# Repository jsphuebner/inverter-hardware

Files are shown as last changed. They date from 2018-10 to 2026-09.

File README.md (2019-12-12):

# inverter-hardware
Eagle schematics of inverter main board, sensor boards and gate drivers

# License
Attribution-ShareAlike 4.0 International
https://creativecommons.org/licenses/by-sa/4.0/legalcode

You musn't change the copyright info (J. Huebner and openinverter.org) on the silkscreen in size location or content.

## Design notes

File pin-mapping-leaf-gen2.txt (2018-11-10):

Connection diagram of CN001
Diagram found here: http://productions.8dromeda.net/c55-leaf-inverter-protocol.html
+-----------------------------------+  +------------+
| 47   46   21 20 19 18 17 16 15 14 |  |       x  x |
|           29 28 27 26 25  x 23 22 |  |  6 x  x  x |
| 49   48    x  x  x  x  x  x  x  x |  | 10 x  x  x |
|           45 44 43 42 41 40 39 38 |  |    x  x  x |
+-----------------------------------+  +------------+

- 6 = OUT_BRAKE
- 10 = IN_BMS
- 14 = CANH *
- 15 = CANL *
- 16 = IN_FORWARD
- 17 = RES_S2 *
- 18 = RES_S4 *
- 19 = RES_R1 *
- 20 = RES_S1 *
- 21 = RES_S3 *
- 22 = IN_START
- 23 = IN_BRAKE
- 25 = IN_REVERSE
- 26 = 5V
- 27 = RES_R2 (GND) *
- 28 = THROTTLE2
- 29 = THROTTLE1
- 38 = IN_CRUISE
- 39 = OUT_PWM
- 40 = OUT_ERR
- 41 = OUT_OVTG
- 42 = OUT_DCSW * (! 12V input on original harness, make sure not to connect to 12V but to DC switch!)
- 43 = OUT_PRE
- 44 = MTEMP1 *
- 45 = MTEMP2 *
- 46 = 12V *
- 47 = GND *
- 48 = 12V *
- 49 = GND *
Only pins with * are populated on the OEM wire harness

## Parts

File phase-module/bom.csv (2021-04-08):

Ref | Part | Value | Remarks
IC1,IC2 | 1ED3124MU12HXUMA1
C1, C2, C3, C5 | C0603 | 1uF
D1 | SMB | CMR1-10 TR13 PBFREE | Any high voltage diode 1A
R1,R2,R3,R4,R6,R7,R9,R10 | R0603 | 10Ω | Gate resistors, application dependent
IC3 | MLX91206LDC-CAH-004-TU
R5 | R0603 | 3k3
R8 | R0603 | 6k8 | Not needed on V3 mainboards

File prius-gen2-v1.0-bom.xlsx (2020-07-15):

Designator | Comment | Package | LCSC Part #
ALIVE, PWR | LED_0603_GN | CHIPLED-0805 | C84256
C7, C22, C27, C33, C43 | 10uF | C0805 | C15850
C1, C2, C3, C35, C36 | 1nF | C0603 | C46653
C13, C23 | 100uF | SMD-ECAP-6.3X7.7 | C176675 | e
C28, C30 | 22p | C0603 | C1804
C4, C5, C6, C8, C9, C10, C11, C12, C14, C15, C16, C17, C18, C20, C21, C24, C25, C37, C41, C42 | 1uF | C0603 | C28323
C19, C26, C29, C31, C32, C34 | 22n | C0603 | C21122
D1, D2 | CDBA540-HF | SMB | C22452
IC7 | MP2359DJ-LF-Z | TSOT-23-6 | C14259
IC3 | TDA2822D | SO08 | C73296 | e
IC5 | SN65HVD230 | SO08 | C12084
IC1 | STM32F103RBT6 | LQFP-64_10.0x10.0x0.5P | C8735
IC6 | ULN2003AD | SO16 | C7512
IC4 | MCP6002T-I/SN | SO08 | C7377
IC2 | AMS1117-3.3 | SOT-223 | C6186
L2, L3 | 10uH | L0805 | C1046
L1 | 6.8uH | L1210 | C87559 | e
Q3 | 8MHz | SMD-5032_2P | C115962
R19 | 220Ω | R0603 | C22962
R12, R14, R15, R20, R25 | 1.2KΩ | R0603 | C22765
R1, R2, R13, R16, R21, R32, R33 | 510Ω | R0603 | C23193
R8, R9, R10, R17, R18, R22, R23, R24, R27, R30, R35, R40, R50, R51, R52, R53, R54, R55, R56 | 10KΩ | R0603 | C17414
R3, R4, R6, R7, R29, R31, R34 | 3.3KΩ | R0603 | C26010
R5, R11 | 4.7KΩ | R0603 | C17673
R42, R49 | 4.7Ω | R0603 | C23164
R26, R36, R37, R38, R39, R47, R48 | 100kΩ | R0603 | C25803
R28 | 56kΩ | R0603 | C23206
Q1, Q2 | AP9T18GH-HF | TO-252-2 | C124546 | e
C38, C39 | 100nF | C0603 | C14663
R44, R46 | 15kΩ | R0603 | C22809
R43, R45 | 33kΩ | R0603 | C4216
R41 | 120Ω | R0603 | C22787

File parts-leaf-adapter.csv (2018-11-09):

Name | Value | Part #
C1 | 1µ
C2 | 1µ
CN001 |  | 1939561-3 (unobtanium - salavage needed)
CN101 |  | GT8E-5P-DS
CN151 |  | GT8E-12DP-DS
CN501 |  | GT8E-16DP-DS
CN601 |  | GT8E-8P-DS
IC1 | 74*00
R1 | 120
R2 | 10k
R3 | 10k
R4 | 10k
R5 | 10k
R7 | 47k
R8 | 47k
R9 | 1k
R10 | 1k

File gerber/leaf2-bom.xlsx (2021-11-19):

Designator | Comment | Package | LCSC Part #
C1, C2 | 1uF | C0805 | C28323
IC1 | MC74HC1G08 | SOT-23-5 | C108694
R2, R3, R4, R5 | 10KΩ | R0603 | C17414
R7, R8 | 47KΩ | R0603 | C25819
R9, R10 | 1.2KΩ | R0603 | C22765

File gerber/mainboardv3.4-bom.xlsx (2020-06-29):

Designator | Comment | Package | LCSC Part #
ALIVE, PWR | LED_0603_GN | CHIPLED-0805 | C84256
C1, C2, C22, C46 | 10uF | C0805 | C15850
C11, C12, C12, C38, C41, C42 | 1nF | C0603 | C46653
C8 | 470uF | SMD-ECAP-10x10 | C176672 | e
C20 | 470uF | SMD-ECAP-6.3X7.7 | C134738 | e
C45 | 330uF | SMD-ECAP-6.3X7.7 | C134823 | e
C26, C27 | 22p | C0603 | C1804
C3, C4, C5, C6, C7, C9, C10, C13, C14, C15, C16, C17, C19, C21, C23, C24, C25, C28, C29, C30, C31, C32, C33, C39, C40, C43, C48 | 1uF | C0603 | C28323
C34, C35, C36, C37, C44, C47 | 22n | C0603 | C21122
D1, D2 | CDBA540-HF | SMB | C22452
D3 | SBR1A40S3-7 | SOD-323F | C2128
IC1 | LM2596S | TO263-5 | C10002
IC2 | TDA2822D | SO08 | C73296 | e
IC3 | SN65HVD230 | SO08 | C12084
IC4 | STM32F103RBT6 | LQFP-64_10.0x10.0x0.5P | C8735
IC5 | MIC2288YD5 | SOT23-5L | C7722
IC6 | ULN2003AD | SO16 | C7512
IC7 | LM2901 | SO14 | C142961 | e
IC8 | AMS1117-3.3 | SOT-223 | C6186
IC9 | SN74LVC1G10 | SOT-23-6 | C258149 | e
L1, L3 | 10uH | L0805 | C1046
L4 | 10uH | L1210 | C86069 | e
L2 | 47uH | SMD-PIND-12.5x12.5x8_2.9x5.4 | C169389 | e
Q1 | 8MHz | SMD-5032_2P | C115962
R1 | 220Ω | R0603 | C22962
R10, R12, R13, R19, R23, R26, R27, R29 | 1.2KΩ | R0603 | C22765
R11, R15, R16, R17, R18, R32, R33, R36, R40 | 510Ω | R0603 | C23193
R14,R20, R21, R22, R24, R25, R31, R37, R38, R39, R41, R43, R45, R46, R47 | 10KΩ | R0603 | C17414
R2, R3, R3, R4, R6, R7, R8, R9, R35, R42, R44, R48, R49 | 3.3KΩ | R0603 | C26010
R5, R50, R51 | 4.7KΩ | R0603 | C17673
R52 | 10Ω | R0603 | C22859
T1 | AP9T18GH-HF | TO-252-2 | C124546 | e

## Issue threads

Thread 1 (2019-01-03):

Gate driver missing

alberto-cesare, 2019-01-03:
Hi Johannes,

thanks for sharing this amazing work.
I noticed that gate driver board, schematic and bom is missing from the repo.
I found the schematic on your site, but there is no name for the DC/DC converter and the pcb.
Can you please upload this design?

Many many thanks!
Alberto

jsphuebner, 2019-01-03:
Hi Alberto,

thanks for pointing it out. I added the part numbers and uploaded the files to the repo.

Johannes

Closed 2019-01-03.

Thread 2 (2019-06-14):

Revision 3

gimbas, 2019-06-14:
Greetings, i was under the impression you made your Revision 3 leaf adapter boards open source also, will the design files be available?
I was looking for the pinout of the leaf inverter connectors.

jsphuebner, 2019-07-25:
The design files vor Rev3 main board will be released as soon as I have sold off my stock.
The adapter board is leaf_adapter.fpc and opens with https://www.freepcb.com/

Closed 2019-12-29.

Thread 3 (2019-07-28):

Add License file

DOSputin, 2019-07-28:
A `LICENSE` including the full language of the chosen licensing scheme should be included as a separate file in the code repository.

DOSputin, 2019-07-28:
Reading the CC license, it says

> indicate the Licensed Material is licensed under this Public License, and include the text of, or the URI or hyperlink to, this Public License.

So it seems that putting the link the readme satisfies this particular license terms.

will close issue now.

jsphuebner, 2019-07-28:
Very good, less to do :) Thanks.

Closed 2019-07-28.

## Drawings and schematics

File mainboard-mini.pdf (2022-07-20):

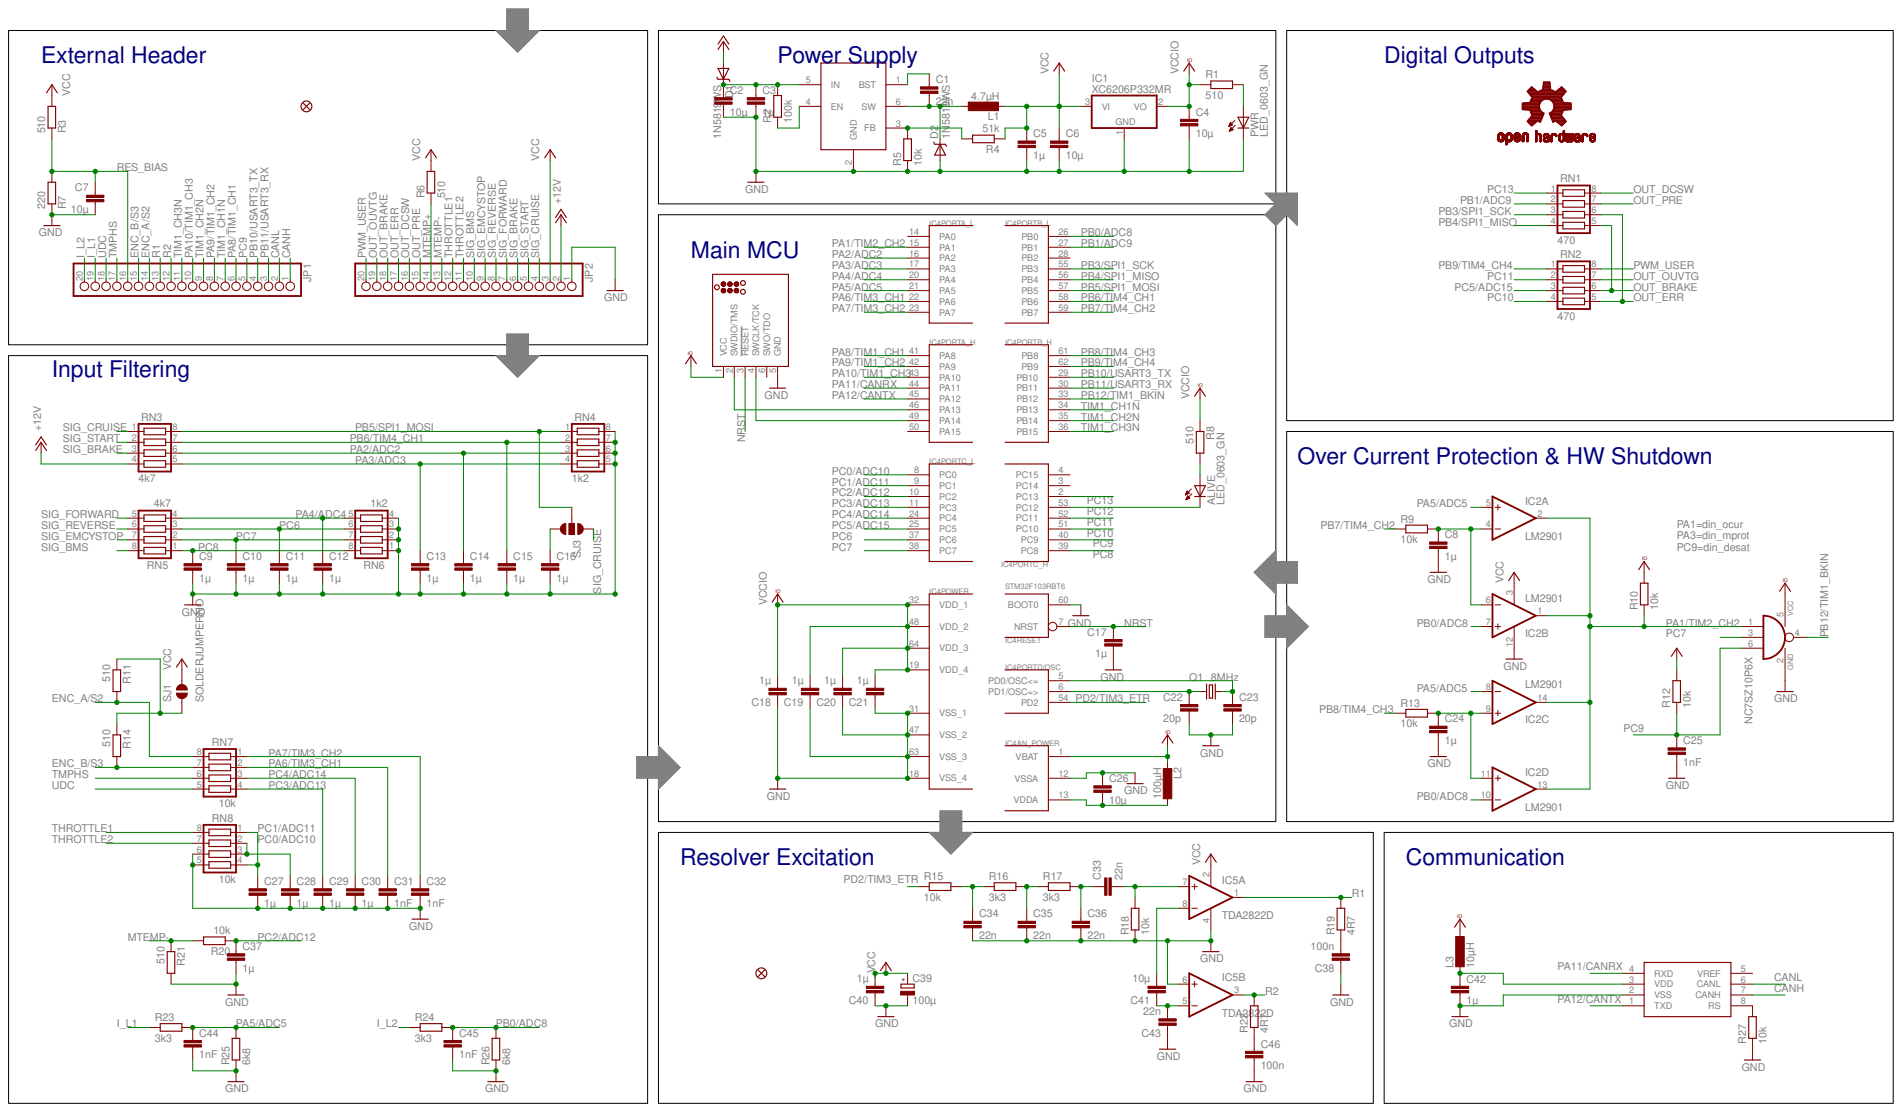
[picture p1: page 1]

IO Over Current Protection & HW Shutdown

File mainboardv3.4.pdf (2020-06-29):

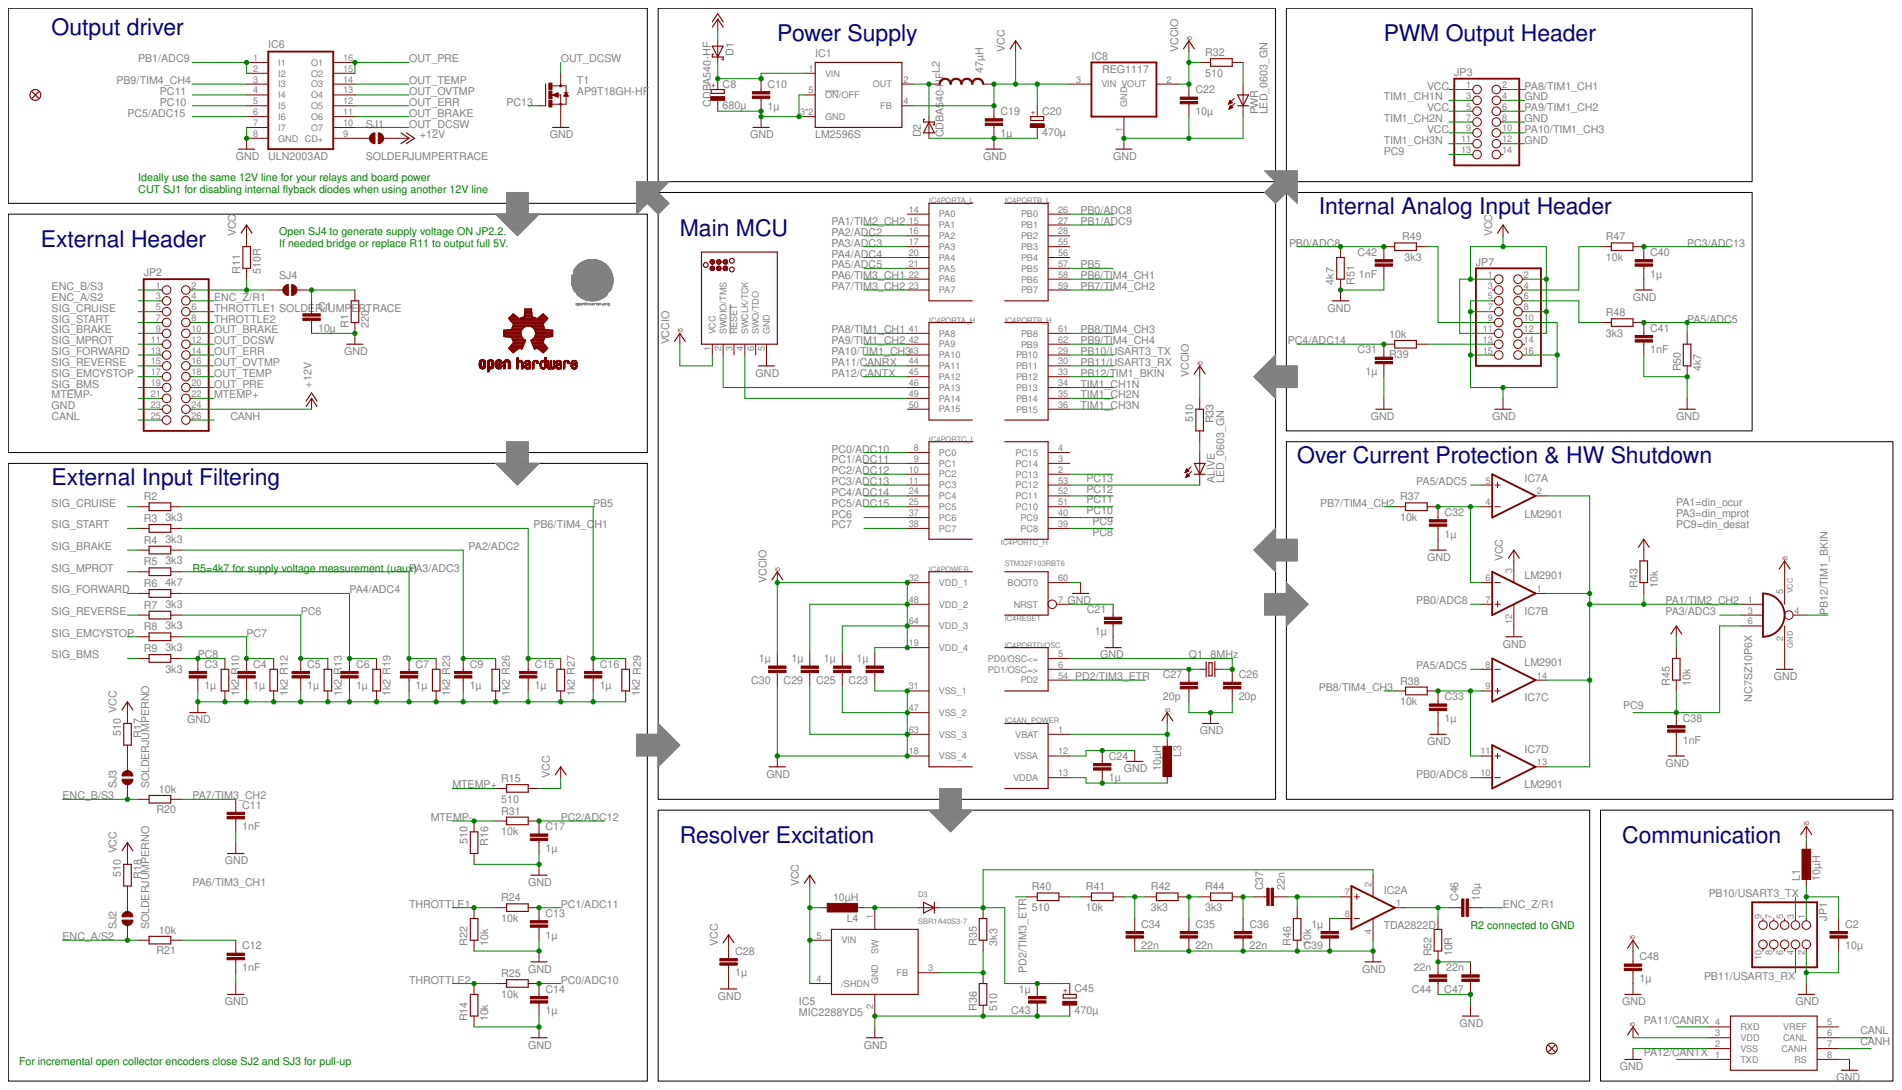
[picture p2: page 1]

Ideally use the same 12V line for your relays and board power CUT SJ1 for disabling internal flyback diodes when using another 12V line

Internal Analog Input Header

Open SJ4 to generate supply voltage ON JP2.2.
If needed bridge or replace R11 to output full 5V.

Over Current Protection & HW Shutdown

For incremental open collector encoders close SJ2 and SJ3 for pull-up

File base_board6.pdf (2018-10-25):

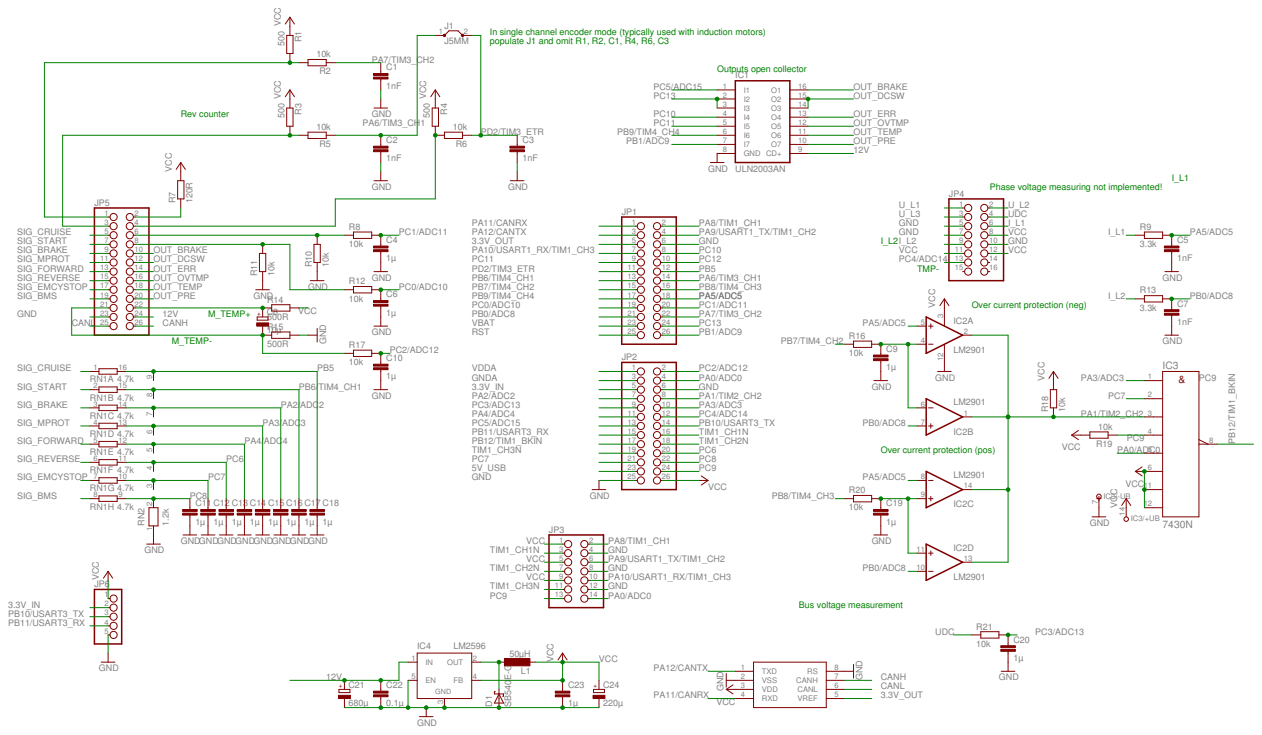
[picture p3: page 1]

In single channel encoder mode (typically used with induction motors) populate J1 and omit R1, R2, C1, R4, R6, C3

Phase voltage measuring not implemented!

Over current protection (pos)

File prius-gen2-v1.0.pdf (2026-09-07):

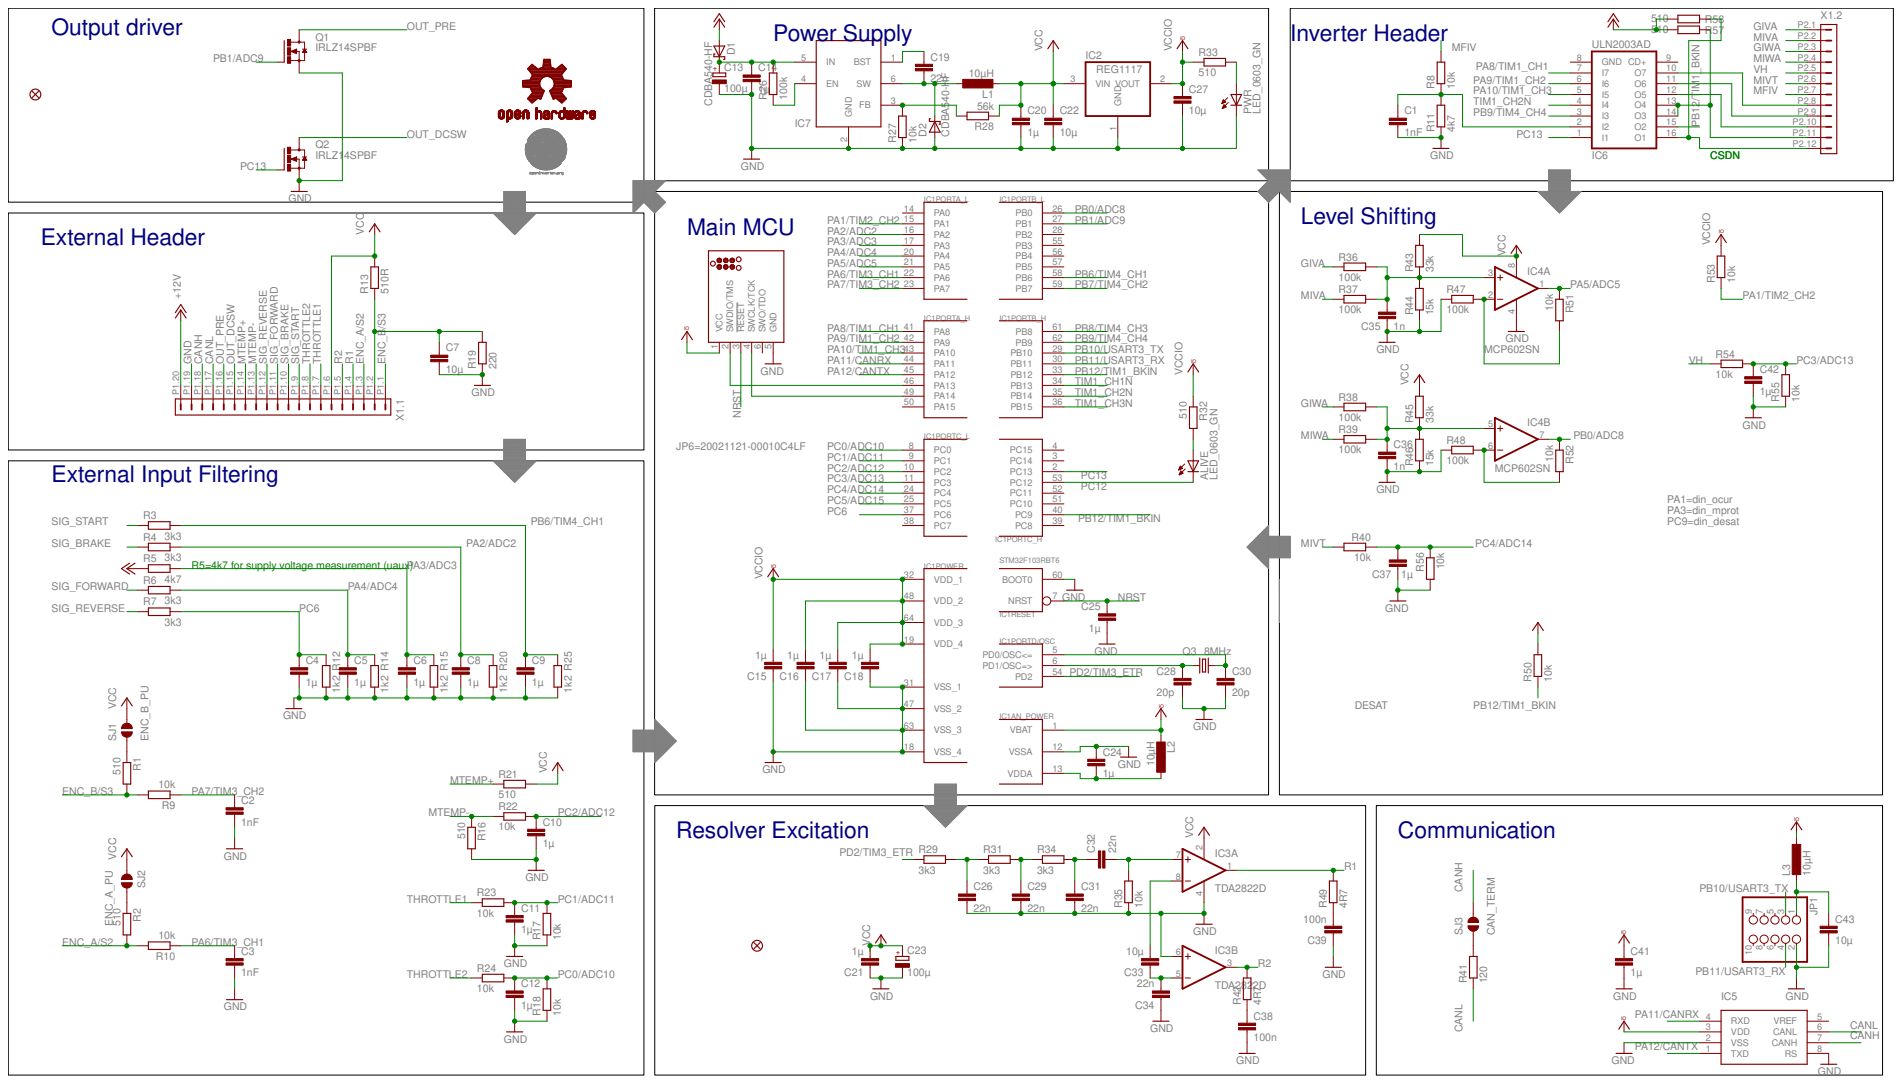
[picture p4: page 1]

Level Shifting Main MCU

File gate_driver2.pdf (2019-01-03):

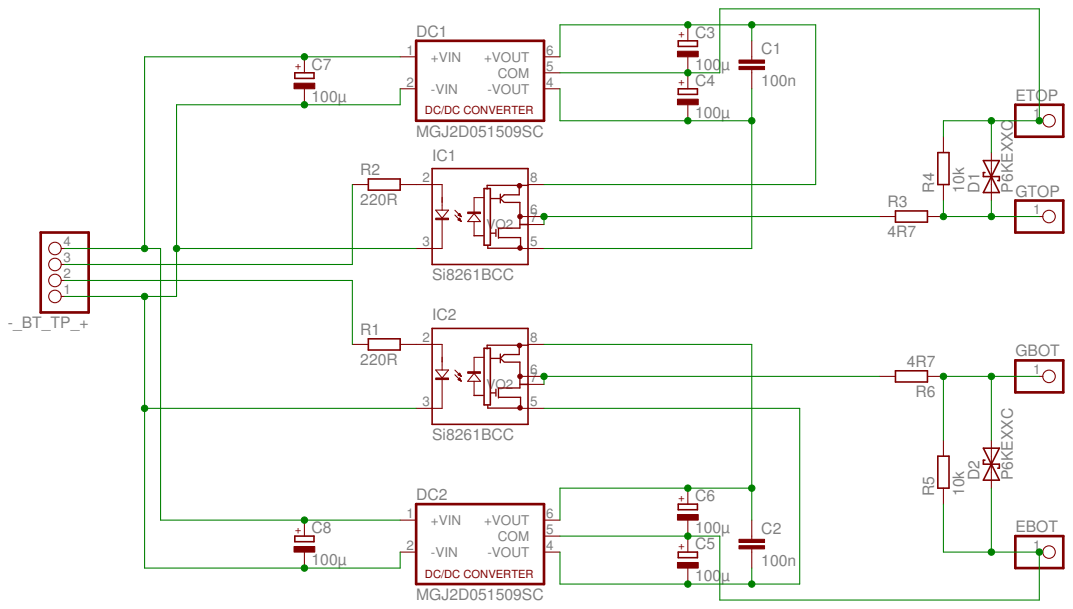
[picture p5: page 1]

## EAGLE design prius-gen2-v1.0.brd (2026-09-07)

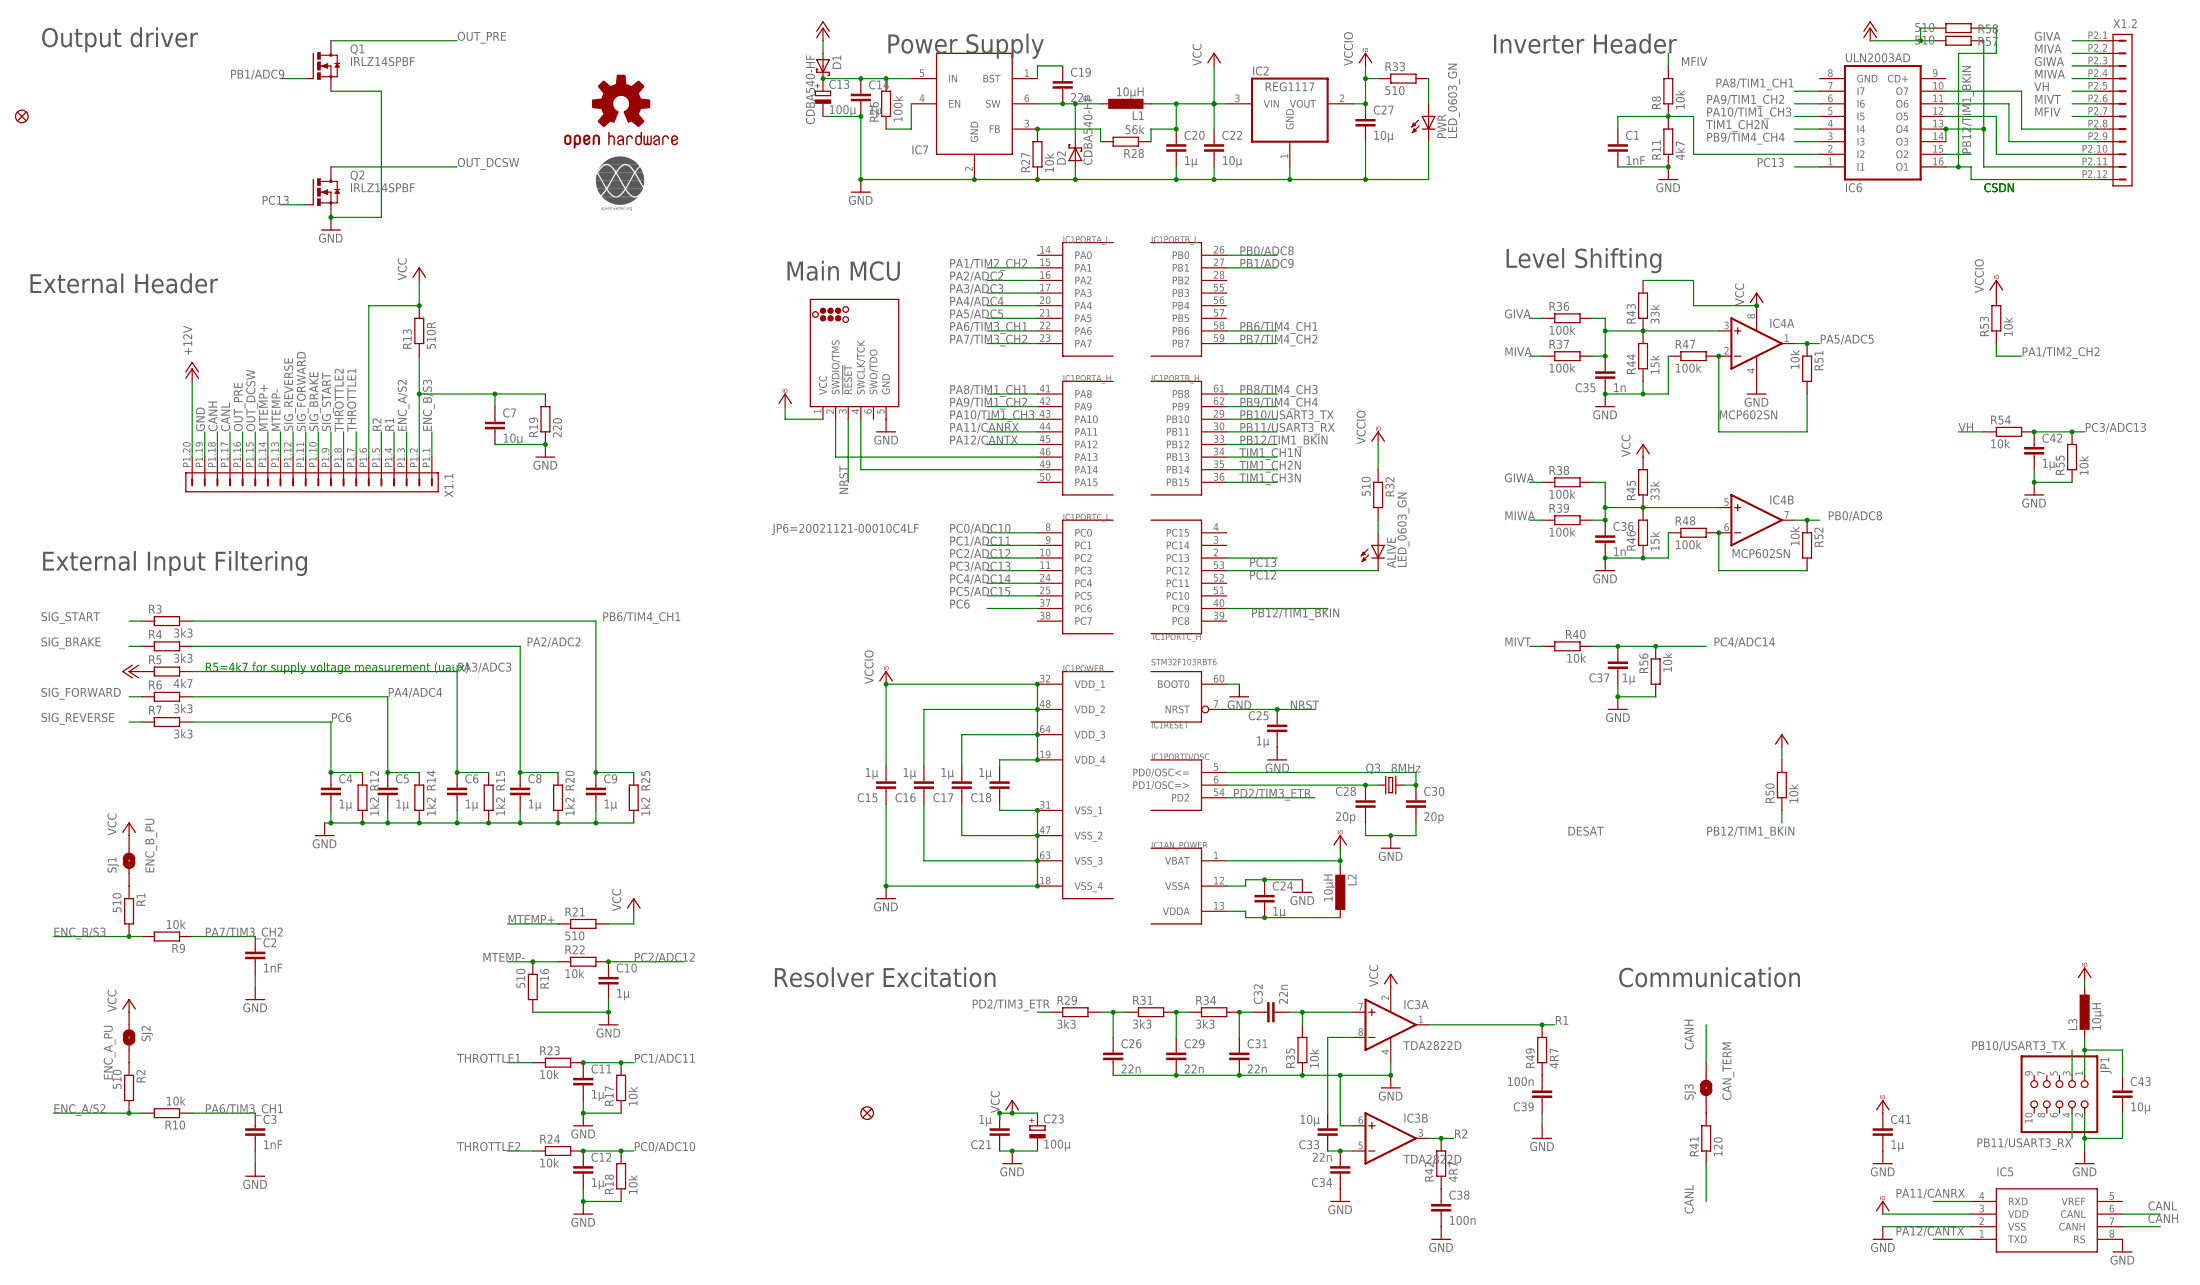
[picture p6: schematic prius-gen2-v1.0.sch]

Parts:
ALIVE: LED_0603_GN; SML0805
C1, C2, C3: 1nF; C0603
C4, C5, C6, C8, C9, C10, C11, C12, C14, C15, C16, C17, C18, C20, C21, C24, C25, C37, C41, C42: 1µ; C0603
C7, C22, C27, C33, C43: 10µ; C0805
C13, C23: 100µ; UD-6,3X7,7_NICHICON
C19, C26, C29, C31, C32, C34: 22n; C0603
C28, C30: 20p; C0603
C35, C36: 1n; C0603
C38, C39: 100n; C0603
D1, D2: CDBA540-HF; SMB
FID1, FID2: FIDUCIAL1X2.5; FIDUCIAL-1X2.5
IC1: STM32F103RBT6; TQFP64
IC2: REG1117; SOT223
IC3: TDA2822D; SO08
IC4: MCP602SN; SO08
IC5: SN65HVD230; SO08
IC6: ULN2003AD; SO16
IC7: MB2359DJ; SOT23-6
J1: TC2030_SWD-MCP; TC2030-MCP
JP1: PINHD-2X5/90; 2X05/90
L1: 10µH; L2825P
L2, L3: 10µH; L2012C
LOGO1: OSHW-LOGOM; OSHW-LOGO-M
PWR: LED_0603_GN; SML0805
Q1, Q2: IRLZ14SPBF; D-PAK_TO252AA
Q3: 8MHz; CRYSTAL-TXC-7A
R1, R2, R16, R21, R32, R33, R57, R58: 510; R0603
R3, R4, R6, R7, R29, R31, R34: 3k3; R0603
R5, R11: 4k7; R0603
R8, R9, R10, R17, R18, R22, R23, R24, R27, R35, R40, R50, R51, R52, R53, R54, R55, R56: 10k; R0603
R12, R14, R15, R20, R25: 1k2; R0603
R13: 510R; R0603
R19: 220; R0603
R26, R36, R37, R38, R39, R47, R48: 100k; R0603
R28: 56k; R0603
R41: 120; R0603
R42, R49: 4R7; R0603
R43, R45: 33k; R0603
R44, R46: 15k; R0603
SJ1: ENC_B_PU; SJ_2S-NO
SJ2: ENC_A_PU; SJ_2S-NO
SJ3: CAN_TERM; SJ_2S-NO
U$1: OI-LOGO; OI_LOGO
X1: 5810132011

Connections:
+12V: D1.A, R5.1, R57.1, R58.1, X1.P1.20 (20)
CANH: IC5.7 (CANH), SJ3.2, X1.P1.18 (18)
CANL: IC5.6 (CANL), R41.1, X1.P1.17 (17)
ENC_A/S2: R2.2, R10.2, X1.P1.3 (3)
ENC_B/S3: R1.2, R9.2, X1.P1.1 (1)
GIVA: R36.1, X1.P2.1 (1)
GIWA: R38.1, X1.P2.3 (3)
GND: C1.2, C2.2, C3.2, C4.2, C5.2, C6.2, C7.2, C8.2, C9.2, C10.2, C11.2, C12.2, C13.-, C14.2, C15.1, C16.1, C17.1, C18.1, C20.2, C21.1, C22.2, C23.-, C24.1, C25.2, C26.2, C27.2, C28.2, C29.2, C30.2, C31.2, C34.1, C35.2, C36.2, C37.2, C38.2, C39.1, C41.2, C42.2, C43.2, D2.A, IC1.12 (VSSA), IC1.18 (VSS_4), IC1.31 (VSS_1), IC1.47 (VSS_2), IC1.60 (BOOT0), IC1.63 (VSS_3), IC2.1 (GND), IC3.4 (V-), IC3.6 (+IN), IC4.4 (V-), IC5.2 (VSS), IC5.8 (RS), IC6.8 (GND), IC7.2 (GND), J1.5 (GND), JP1.2, PWR.C, Q1.3 (S), Q2.3 (S), R11.1, R12.1, R14.1, R15.1, R16.2, R17.1, R18.1, R19.1, R20.1, R25.1, R27.1, R35.1, R44.1, R46.1, R47.1, R48.1, R55.1, R56.2, X1.P1.19 (19)
MFIV: R8.2, X1.P2.7 (7)
MIVA: R37.1, X1.P2.2 (2)
MIVT: R40.2, X1.P2.6 (6)
MIWA: R39.1, X1.P2.4 (4)
MTEMP+: R21.1, X1.P1.14 (14)
MTEMP-: R16.1, R22.1, X1.P1.13 (13)
unnamed: IC6.12 (O5), X1.P2.10 (10)
unnamed: C28.1, IC1.6 (PD1/OSC=>), Q3.P$1 (1)
unnamed: C13.+, C14.1, D1.C, IC7.5 (IN), R26.2
unnamed: C30.1, IC1.5 (PD0/OSC<=), Q3.P$2 (2)
unnamed: C19.1, IC7.1 (BST)
unnamed: IC1.46 (PA13), J1.2 (SWDIO/TMS)
unnamed: C24.2, IC1.13 (VDDA), L2.1
unnamed: IC7.4 (EN), R26.1
unnamed: IC1.49 (PA14), J1.4 (SWCLK/TCK)
unnamed: C33.1, C34.2, IC3.5 (-IN)
unnamed: C39.2, R49.1
unnamed: C33.2, IC3.8 (-IN)
unnamed: IC7.3 (FB), R27.2, R28.2
unnamed: C19.2, D2.C, IC7.6 (SW), L1.1
unnamed: IC6.11 (O6), X1.P2.9 (9)
unnamed: IC6.10 (O7), X1.P2.8 (8)
unnamed: C29.1, R31.2, R34.1
unnamed: C31.1, C32.1, R34.2
unnamed: C32.2, IC3.7 (+IN), R35.2
unnamed: R2.1, SJ2.2
unnamed: R1.1, SJ1.1
unnamed: PWR.A, R33.2
unnamed: ALIVE.A, R32.2
unnamed: C1.1, IC6.2 (I2), R8.1, R11.2
unnamed: IC6.16 (O1), R58.2, X1.P2.12 (12)
unnamed: R41.2, SJ3.1
unnamed: C38.1, R42.1
unnamed: C43.1, JP1.1, L3.2
unnamed: IC6.13 (O4), IC6.14 (O3), R57.2, X1.P2.11 (11)
unnamed: C26.1, R29.2, R31.1
unnamed: C36.1, IC4.5 (+IN), R38.2, R39.2, R45.1, R46.2
unnamed: C35.1, IC4.3 (+IN), R36.2, R37.2, R43.1, R44.2
unnamed: IC4.2 (-IN), R47.2, R51.2
unnamed: IC4.6 (-IN), R48.2, R52.2
NRST: C25.1, IC1.7 (NRST), J1.3 (!RESET)
OUT_DCSW: Q2.4 (D), X1.P1.15 (15)
OUT_PRE: Q1.4 (D), X1.P1.16 (16)
PA1/TIM2_CH2: IC1.15 (PA1), R53.1
PA2/ADC2: C8.1, IC1.16 (PA2), R4.2, R20.2
PA3/ADC3: C6.1, IC1.17 (PA3), R5.2, R15.2
PA4/ADC4: C5.1, IC1.20 (PA4), R6.2, R14.2
PA5/ADC5: IC1.21 (PA5), IC4.1 (OUT), R51.1
PA6/TIM3_CH1: C3.1, IC1.22 (PA6), R10.1
PA7/TIM3_CH2: C2.1, IC1.23 (PA7), R9.1
PA8/TIM1_CH1: IC1.41 (PA8), IC6.7 (I7)
PA9/TIM1_CH2: IC1.42 (PA9), IC6.6 (I6)
PA10/TIM1_CH3: IC1.43 (PA10), IC6.5 (I5)
PA11/CANRX: IC1.44 (PA11), IC5.4 (RXD)
PA12/CANTX: IC1.45 (PA12), IC5.1 (TXD)
PB0/ADC8: IC1.26 (PB0), IC4.7 (OUT), R52.1
PB1/ADC9: IC1.27 (PB1), Q1.1 (G)
PB6/TIM4_CH1: C9.1, IC1.58 (PB6), R3.2, R25.2
PB7/TIM4_CH2: IC1.59 (PB7)
PB8/TIM4_CH3: IC1.61 (PB8)
PB9/TIM4_CH4: IC1.62 (PB9), IC6.3 (I3)
PB10/USART3_TX: IC1.29 (PB10), JP1.3
PB11/USART3_RX: IC1.30 (PB11), JP1.4
PB12/TIM1_BKIN: IC1.33 (PB12), IC1.40 (PC9), IC6.15 (O2), R50.1
PC0/ADC10: C12.1, IC1.8 (PC0), R18.2, R24.2
PC1/ADC11: C11.1, IC1.9 (PC1), R17.2, R23.2
PC2/ADC12: C10.1, IC1.10 (PC2), R22.2
PC3/ADC13: C42.1, IC1.11 (PC3), R54.2, R55.2
PC4/ADC14: C37.1, IC1.24 (PC4), R40.1, R56.1
PC5/ADC15: IC1.25 (PC5)
PC6: C4.1, IC1.37 (PC6), R7.2, R12.2
PC12: ALIVE.C, IC1.53 (PC12)
PC13: IC1.2 (PC13), IC6.1 (I1), Q2.1 (G)
PD2/TIM3_ETR: IC1.54 (PD2), R29.1
R1: IC3.1 (OUT), R49.2, X1.P1.4 (4)
R2: IC3.3 (OUT), R42.2, X1.P1.5 (5)
S4/S1: C7.1, R13.1, R19.2, X1.P1.2 (2)
SIG_BRAKE: R4.1, X1.P1.10 (10)
SIG_FORWARD: R6.1, X1.P1.11 (11)
SIG_REVERSE: R7.1, X1.P1.12 (12)
SIG_START: R3.1, X1.P1.9 (9)
THROTTLE1: R23.1, X1.P1.7 (7)
THROTTLE2: R24.1, X1.P1.8 (8)
TIM1_CH1N: IC1.34 (PB13)
TIM1_CH2N: IC1.35 (PB14), IC6.4 (I4)
TIM1_CH3N: IC1.36 (PB15)
VCC: C20.1, C21.2, C22.1, C23.+, IC2.3 (VIN), IC3.2 (V+), IC4.8 (V+), L1.2, R13.2, R21.2, R28.1, R43.2, R45.2, R50.2, SJ1.2, SJ2.1, X1.P1.6 (6)
VCCIO: C15.2, C16.2, C17.2, C18.2, C27.1, C41.1, IC1.1 (VBAT), IC1.19 (VDD_4), IC1.32 (VDD_1), IC1.48 (VDD_2), IC1.64 (VDD_3), IC2.2 (VOUT), IC5.3 (VDD), J1.1 (VCC), L2.2, L3.1, R32.1, R33.1, R53.2
VH: R54.1, X1.P2.5 (5)

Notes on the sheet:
Output driver
Resolver Excitation
External Input Filtering
External Header
Communication
Power Supply
Inverter Header
Level Shifting
Main MCU
R5=4k7 for supply voltage measurement (uaux)
JP6=20021121-00010C4LF
DESAT
IC7
IC5
CSDN

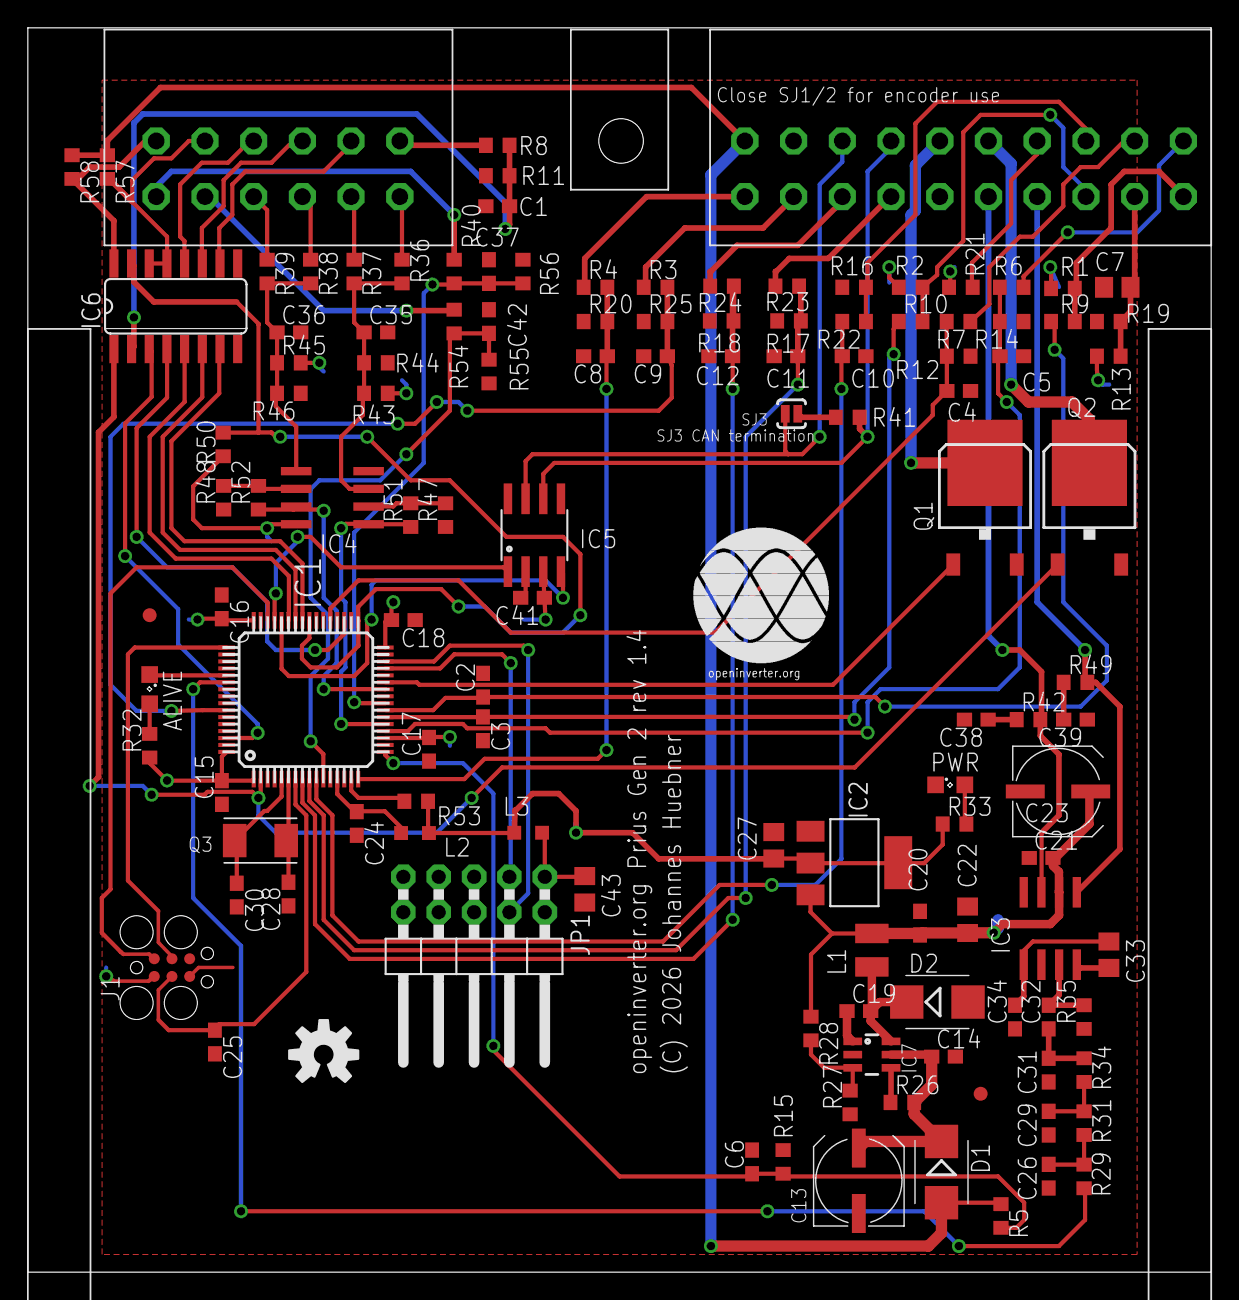
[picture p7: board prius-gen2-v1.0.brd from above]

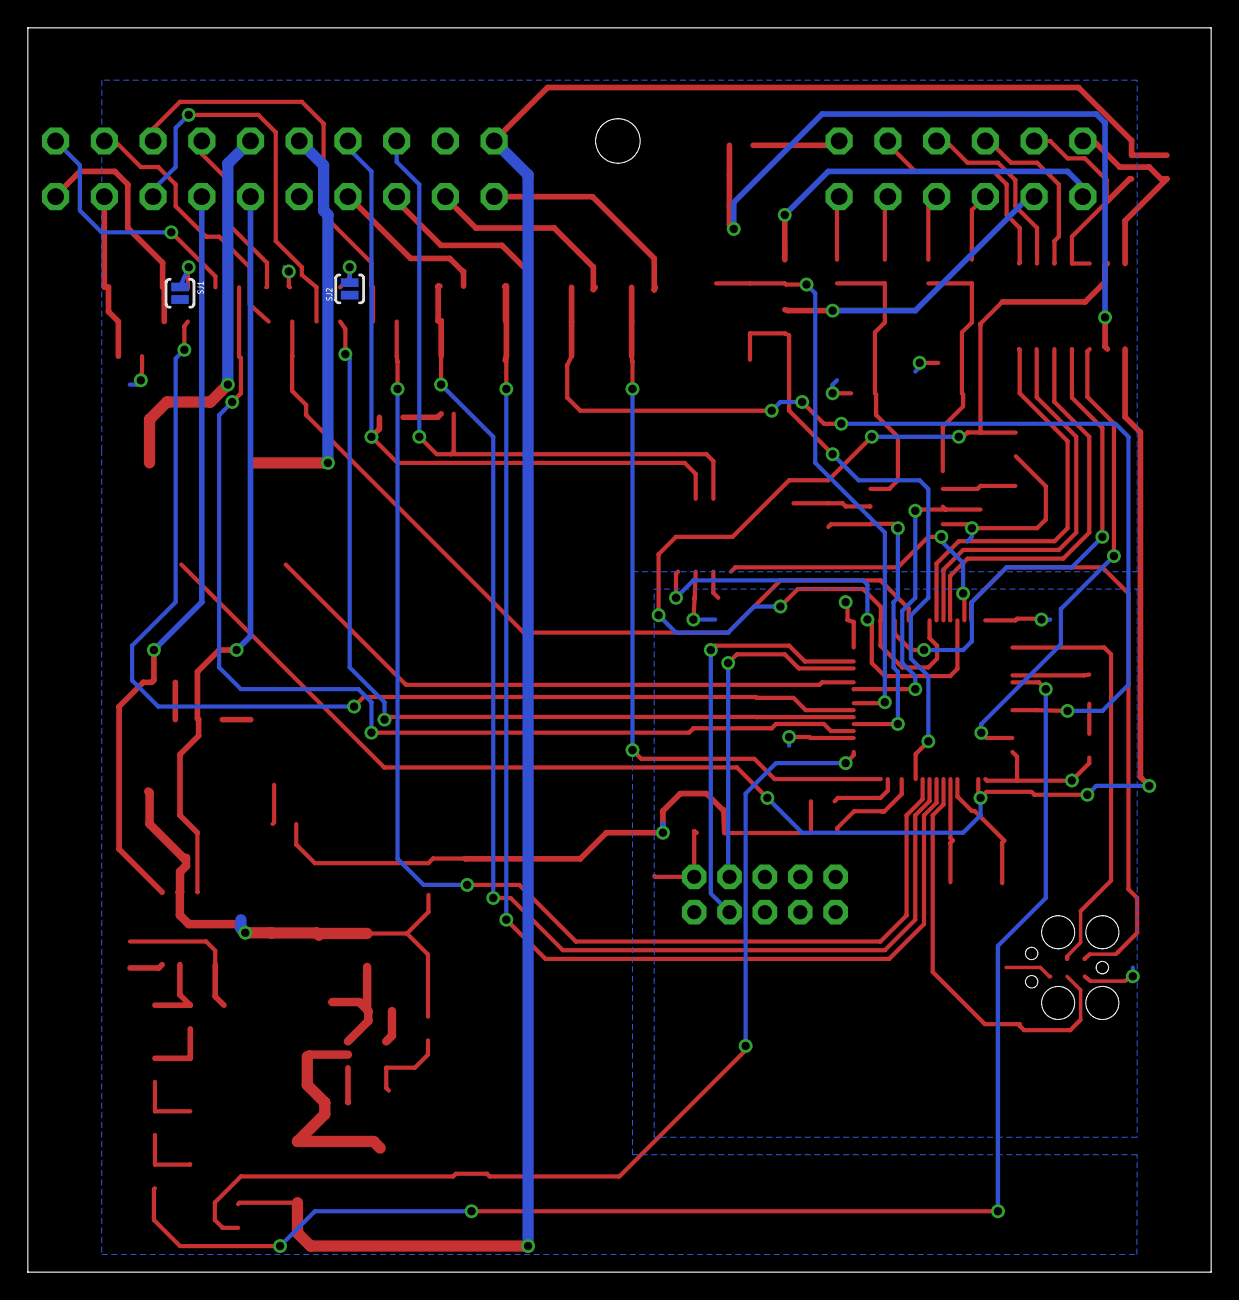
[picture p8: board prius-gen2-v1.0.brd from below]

Board: 2 copper layers, 85.0 x 89.4 mm, 126 parts (2 on the bottom side), 92 nets.

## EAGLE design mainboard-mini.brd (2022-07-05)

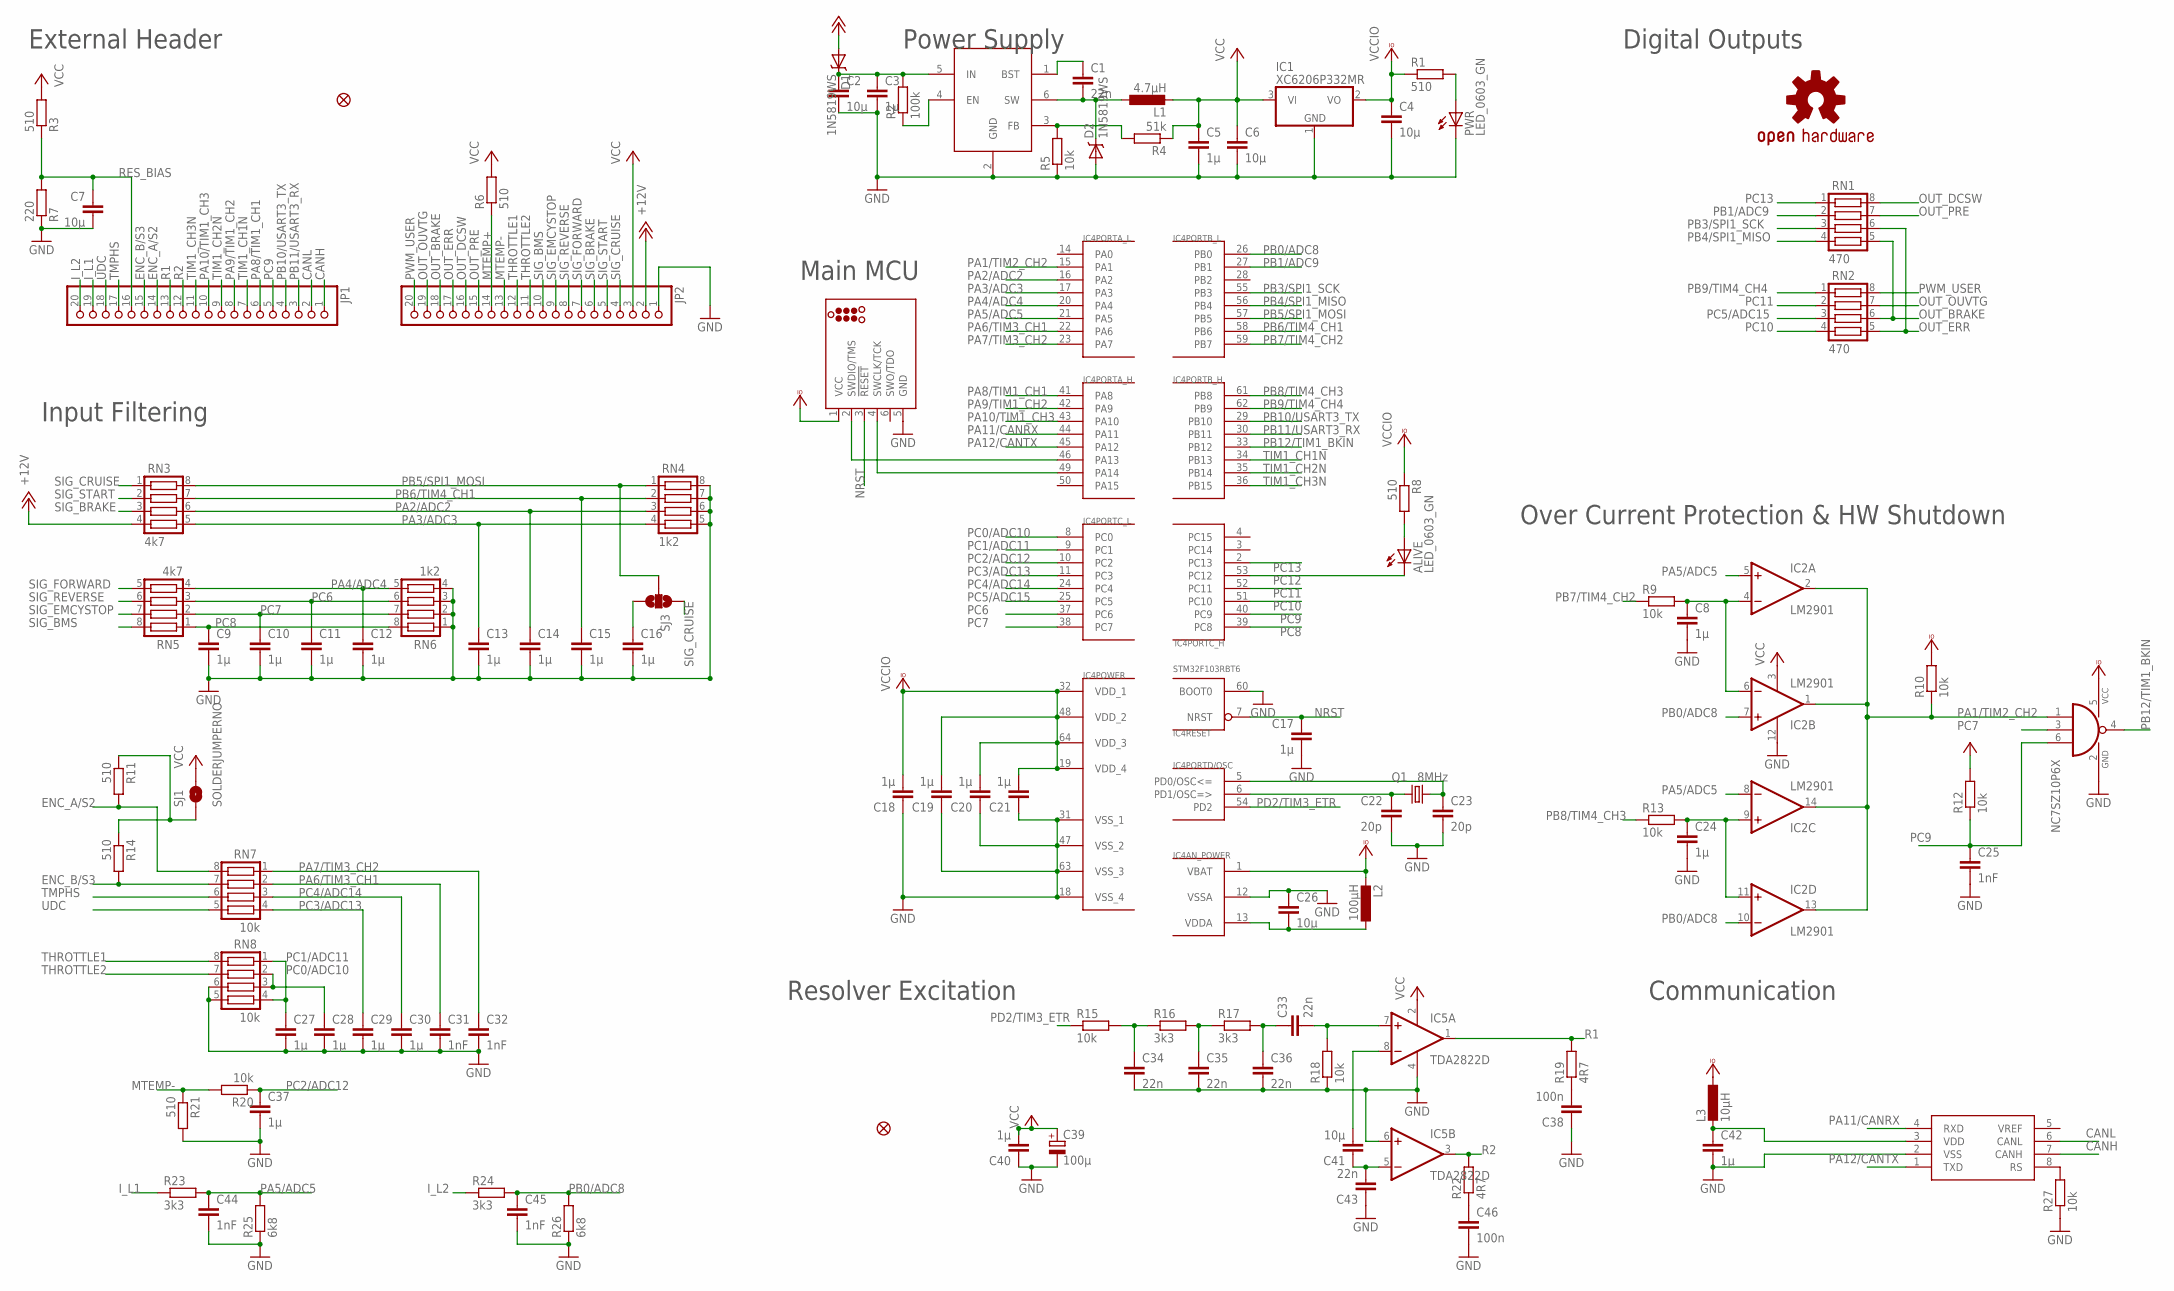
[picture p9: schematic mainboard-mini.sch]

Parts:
ALIVE: LED_0603_GN; SML0805
C1, C33, C34, C35, C36, C43: 22n; C0603
C2, C4, C6, C7, C26, C41: 10µ; C0603
C3, C5, C8, C9, C10, C11, C12, C13, C14, C15, C16, C17, C18, C19, C20, C21, C24, C27, C28, C29, C30, C37, C40, C42: 1µ; C0603
C22, C23: 20p; C0603
C25, C31, C32, C44, C45: 1nF; C0603
C38, C46: 100n; C0603
C39: 100µ; B/3528-21R
D1, D2: 1N5819WS; SOD-323
FID1, FID2: FIDUCIAL1X2.5; FIDUCIAL-1X2.5
IC1: XC6206P332MR; SOT23
IC2: LM2901; SO14
IC3: NC7SZ10P6X; SC70-6
IC4: STM32F103RBT6; TQFP64
IC5: TDA2822D; SO08
IC6: SN65HVD230; SO08
IC7: RT8259GE; SOT23-6
J1: TC2030_SWD-MCP; TC2030-MCP
JP1, JP2: PINHD-1X20; 1X20
L1: 4.7µH; L2825P
L2: 100µH; L2012C
L3: 10µH; L2012C
LOGO1: OSHW-LOGOM; OSHW-LOGO-M
PWR: LED_0603_GN; SML0805
Q1: 8MHz; CRYSTAL-TXC-7A
R1, R3, R6, R8, R11, R14, R21: 510; R0603
R2: 100k; R0603
R4: 51k; R0603
R5, R9, R10, R12, R13, R15, R18, R20, R27: 10k; R0603
R7: 220; R0603
R16, R17, R23, R24: 3k3; R0603
R19, R22: 4R7; R0603
R25, R26: 6k8; R0603
RN1, RN2: 470; CTS742C083
RN3, RN5: 4k7; CTS742C083
RN4, RN6: 1k2; CTS742C083
RN7, RN8: 10k; CTS742C083
SJ1: SOLDERJUMPERNO; SJ_2S-NO
SJ3: SOLDERJUMPER_2WAYPASTE2&3; SJ_3_PASTE2&3

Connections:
+12V: D1.2 (A), JP2.2, RN3.4
CANH: IC6.7 (CANH), JP1.1
CANL: IC6.6 (CANL), JP1.2
ENC_A/S2: JP1.14, R11.2, RN7.8
ENC_B/S3: JP1.15, R14.2, RN7.7
GND: C2.2, C3.2, C4.2, C5.2, C6.2, C7.2, C8.2, C9.2, C10.2, C11.2, C12.2, C13.2, C14.2, C15.2, C16.2, C17.2, C18.1, C19.1, C20.1, C21.1, C22.2, C23.2, C24.2, C25.2, C26.1, C27.2, C28.2, C29.2, C30.2, C31.2, C32.2, C34.2, C35.2, C36.2, C37.2, C38.1, C39.-, C40.1, C42.2, C43.1, C44.2, C45.2, C46.2, D2.2 (A), IC1.1 (GND), IC2.12 (GND), IC3.2 (GND), IC4.12 (VSSA), IC4.18 (VSS_4), IC4.31 (VSS_1), IC4.47 (VSS_2), IC4.60 (BOOT0), IC4.63 (VSS_3), IC5.4 (V-), IC5.6 (+IN), IC6.2 (VSS), IC7.2 (GND), J1.5 (GND), JP2.1, PWR.C, R5.1, R7.1, R18.1, R21.2, R25.1, R26.1, R27.1, RN4.5, RN4.6, RN4.7, RN4.8, RN6.1, RN6.2, RN6.3, RN6.4, RN8.5, RN8.6
I_L1: JP1.19, R23.1
I_L2: JP1.20, R24.1
MTEMP+: JP2.14, R6.1
MTEMP-: JP2.13, R20.2, R21.1
unnamed: C41.1, C43.2, IC5.5 (-IN)
unnamed: C22.1, IC4.6 (PD1/OSC=>), Q1.P$1 (1)
unnamed: C2.1, C3.1, D1.1 (C), IC7.5 (IN), R2.2
unnamed: C23.1, IC4.5 (PD0/OSC<=), Q1.P$2 (2)
unnamed: C1.1, IC7.1 (BST)
unnamed: IC4.46 (PA13), J1.2 (SWDIO/TMS)
unnamed: C26.2, IC4.13 (VDDA), L2.1
unnamed: IC7.4 (EN), R2.1
unnamed: IC4.49 (PA14), J1.4 (SWCLK/TCK)
unnamed: C24.1, IC2.9 (+IN), IC2.11 (+IN), R13.2
unnamed: C38.2, R19.1
unnamed: C41.2, IC5.8 (-IN)
unnamed: IC7.3 (FB), R4.2, R5.2
unnamed: C1.2, D2.1 (C), IC7.6 (SW), L1.1
unnamed: C8.1, IC2.4 (-IN), IC2.6 (-IN), R9.2
unnamed: C42.1, IC6.3 (VDD), L3.2
unnamed: C35.1, R16.2, R17.1
unnamed: C33.1, C36.1, R17.2
unnamed: C33.2, IC5.7 (+IN), R18.2
unnamed: R11.1, R14.1, SJ1.1
unnamed: C16.1, SJ3.3
unnamed: PWR.A, R1.2
unnamed: ALIVE.A, R8.2
unnamed: IC6.8 (RS), R27.2
unnamed: C46.1, R22.1
unnamed: C34.1, R15.2, R16.1
NRST: C17.1, IC4.7 (NRST), J1.3 (!RESET)
OUT_BRAKE: JP2.18, RN1.5, RN2.6
OUT_DCSW: JP2.16, RN1.8
OUT_ERR: JP2.17, RN1.6, RN2.5
OUT_OUVTG: JP2.19, RN2.7
OUT_PRE: JP2.15, RN1.7
PA1/TIM2_CH2: IC2.1 (OUT), IC2.2 (OUT), IC2.13 (OUT), IC2.14 (OUT), IC3.1 (I0), IC4.15 (PA1), R10.1
PA2/ADC2: C14.1, IC4.16 (PA2), RN3.6, RN4.3
PA3/ADC3: C13.1, IC4.17 (PA3), RN3.5, RN4.4
PA4/ADC4: C12.1, IC4.20 (PA4), RN5.4, RN6.5
PA5/ADC5: C44.1, IC2.5 (+IN), IC2.8 (-IN), IC4.21 (PA5), R23.2, R25.2
PA6/TIM3_CH1: C31.1, IC4.22 (PA6), RN7.2
PA7/TIM3_CH2: C32.1, IC4.23 (PA7), RN7.1
PA8/TIM1_CH1: IC4.41 (PA8), JP1.6
PA9/TIM1_CH2: IC4.42 (PA9), JP1.8
PA10/TIM1_CH3: IC4.43 (PA10), JP1.10
PA11/CANRX: IC4.44 (PA11), IC6.4 (RXD)
PA12/CANTX: IC4.45 (PA12), IC6.1 (TXD)
PB0/ADC8: C45.1, IC2.7 (+IN), IC2.10 (-IN), IC4.26 (PB0), R24.2, R26.2
PB1/ADC9: IC4.27 (PB1), RN1.2
PB3/SPI1_SCK: IC4.55 (PB3), RN1.3
PB4/SPI1_MISO: IC4.56 (PB4), RN1.4
PB5/SPI1_MOSI: IC4.57 (PB5), RN3.8, RN4.1, SJ3.2
PB6/TIM4_CH1: C15.1, IC4.58 (PB6), RN3.7, RN4.2
PB7/TIM4_CH2: IC4.59 (PB7), R9.1
PB8/TIM4_CH3: IC4.61 (PB8), R13.1
PB9/TIM4_CH4: IC4.62 (PB9), RN2.1
PB10/USART3_TX: IC4.29 (PB10), JP1.4
PB11/USART3_RX: IC4.30 (PB11), JP1.3
PB12/TIM1_BKIN: IC3.4 (O), IC4.33 (PB12)
PC0/ADC10: C28.1, IC4.8 (PC0), RN8.2, RN8.3
PC1/ADC11: C27.1, IC4.9 (PC1), RN8.1, RN8.4
PC2/ADC12: C37.1, IC4.10 (PC2), R20.1
PC3/ADC13: C29.1, IC4.11 (PC3), RN7.4
PC4/ADC14: C30.1, IC4.24 (PC4), RN7.3
PC5/ADC15: IC4.25 (PC5), RN2.3
PC6: C11.1, IC4.37 (PC6), RN5.3, RN6.6
PC7: C10.1, IC3.3 (I1), IC4.38 (PC7), RN5.2, RN6.7
PC8: C9.1, IC4.39 (PC8), RN5.1, RN6.8
PC9: C25.1, IC3.6 (I2), IC4.40 (PC9), JP1.5, R12.1
PC10: IC4.51 (PC10), RN2.4
PC11: IC4.52 (PC11), RN2.2
PC12: ALIVE.C, IC4.53 (PC12)
PC13: IC4.2 (PC13), RN1.1
PD2/TIM3_ETR: IC4.54 (PD2), R15.1
PWM_USER: JP2.20, RN2.8
R1: IC5.1 (OUT), JP1.13, R19.2
R2: IC5.3 (OUT), JP1.12, R22.2
RES_BIAS: C7.1, JP1.16, R3.1, R7.2
SIG_BMS: JP2.10, RN5.8
SIG_BRAKE: JP2.6, RN3.3
SIG_CRUISE: JP2.4, RN3.1, SJ3.1
SIG_EMCYSTOP: JP2.9, RN5.7
SIG_FORWARD: JP2.7, RN5.5
SIG_REVERSE: JP2.8, RN5.6
SIG_START: JP2.5, RN3.2
THROTTLE1: JP2.12, RN8.8
THROTTLE2: JP2.11, RN8.7
TIM1_CH1N: IC4.34 (PB13), JP1.7
TIM1_CH2N: IC4.35 (PB14), JP1.9
TIM1_CH3N: IC4.36 (PB15), JP1.11
TMPHS: JP1.17, RN7.6
UDC: JP1.18, RN7.5
VCC: C5.1, C6.1, C39.+, C40.2, IC1.3 (VI), IC2.3 (V+), IC5.2 (V+), JP2.3, L1.2, R3.2, R4.1, R6.2, R12.2, SJ1.2
VCCIO: C4.1, C18.2, C19.2, C20.2, C21.2, IC1.2 (VO), IC3.5 (VCC), IC4.1 (VBAT), IC4.19 (VDD_4), IC4.32 (VDD_1), IC4.48 (VDD_2), IC4.64 (VDD_3), J1.1 (VCC), L2.2, L3.1, R1.1, R8.1, R10.2

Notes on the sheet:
Over Current Protection & HW Shutdown
Input Filtering
External Header
Communication
Power Supply
Digital Outputs
Main MCU
Resolver Excitation

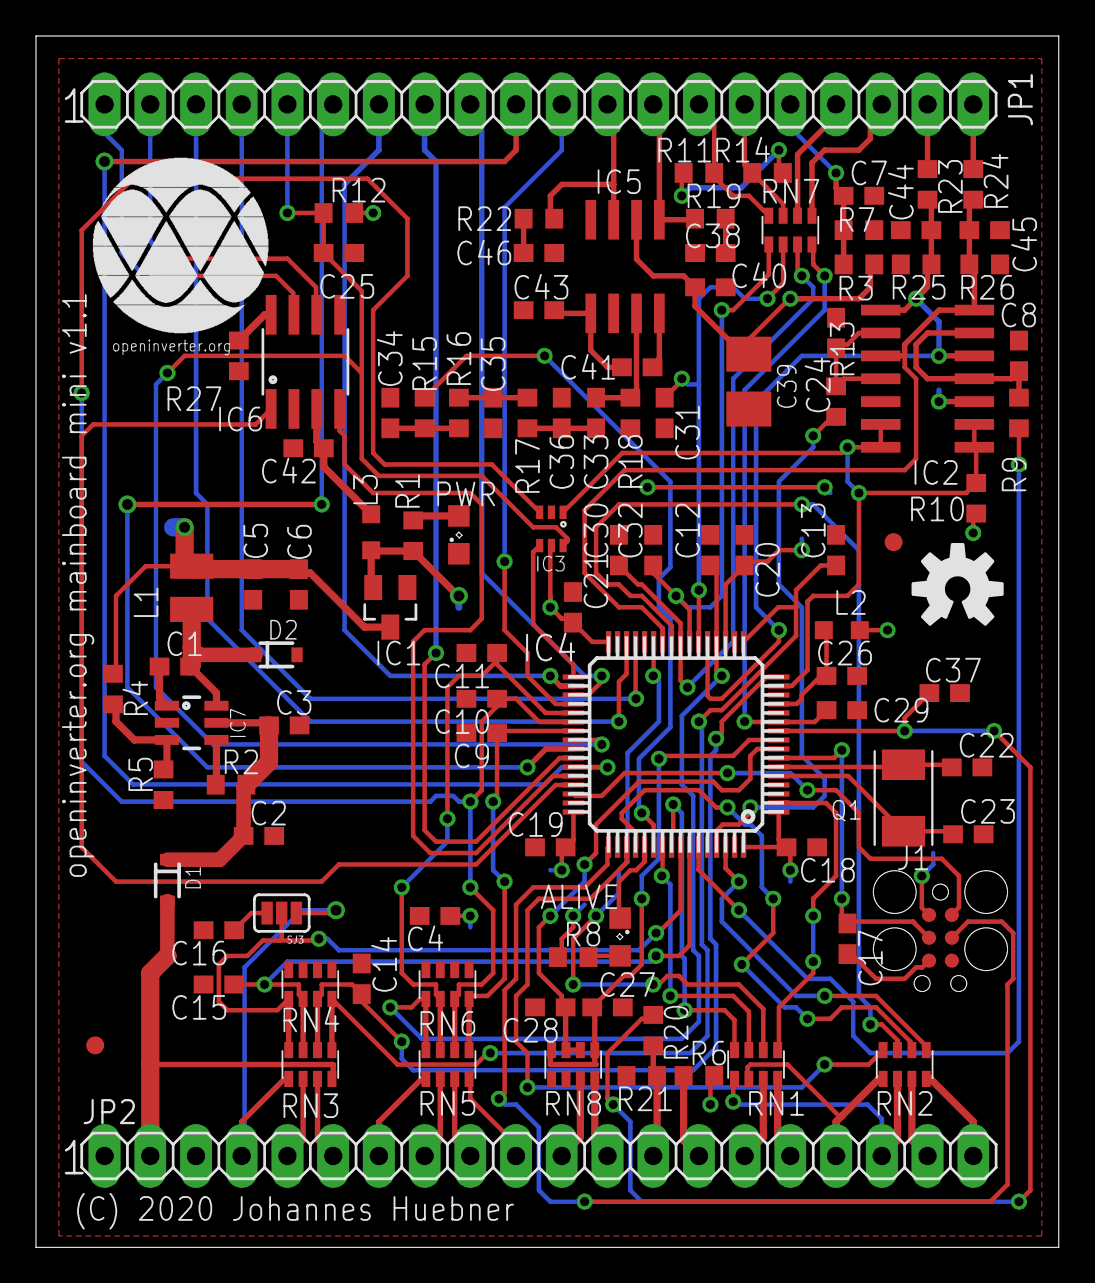
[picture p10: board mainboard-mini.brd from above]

Board: 2 copper layers, 56.8 x 67.3 mm, 105 parts (1 on the bottom side), 101 nets.

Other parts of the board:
U$2: OI_LOGO

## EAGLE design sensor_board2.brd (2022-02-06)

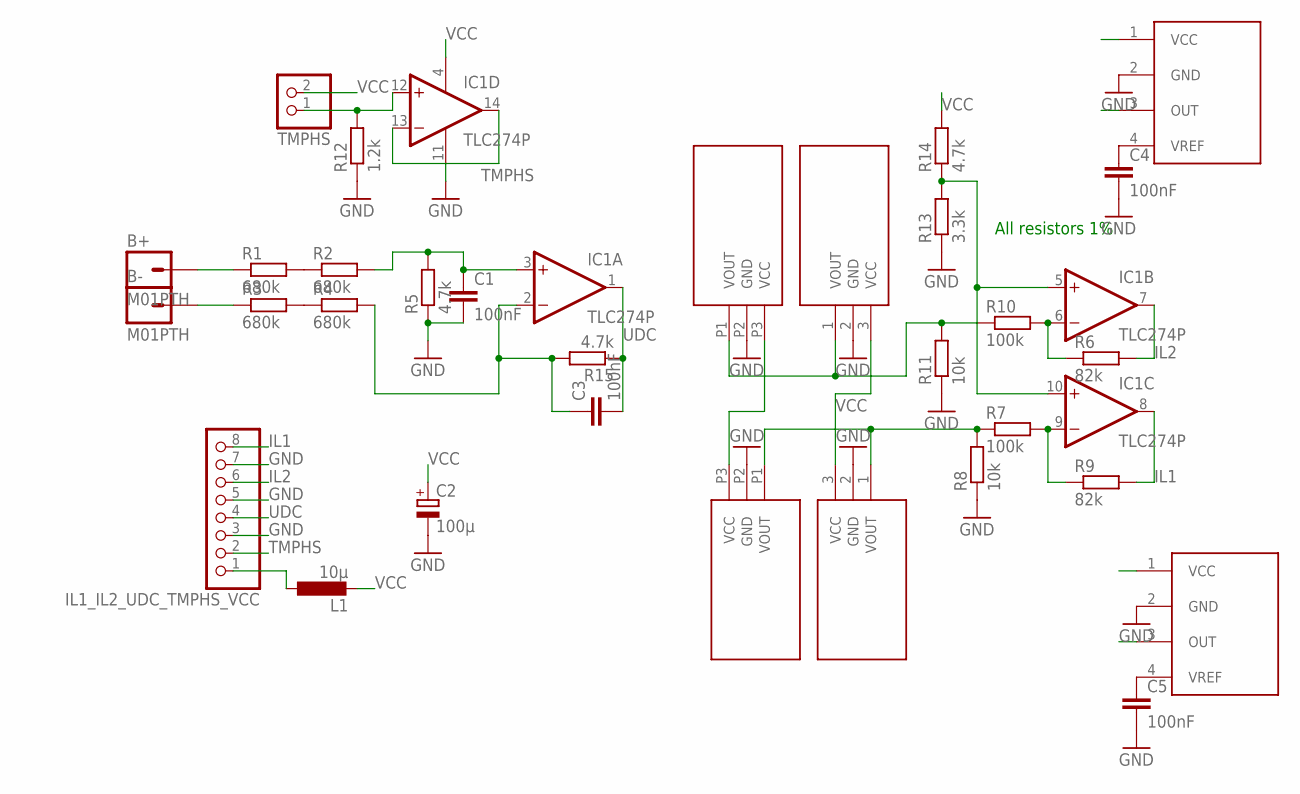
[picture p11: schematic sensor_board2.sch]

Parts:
B+: M01PTH; 1X01
B-: M01PTH; 1X01
C1, C3, C4, C5: 100nF; C025-024X044
C2: 100µ; E2,5-6E
IC1: TLC274P; DIL14
IL1_IL2_UDC_TMPHS_VCC: PINHD-1X8; 1X08
L1: 10µ; 0207/12
R1, R2, R3, R4: 680k; 0207/10
R5, R14, R15: 4.7k; 0207/10
R6, R9: 82k; 0207/10
R7, R10: 100k; 0207/10
R8, R11: 10k; 0207/10
R12: 1.2k; 0207/10
R13: 3.3k; 0207/10
TMPHS: PINHD-1X2; 1X02
U$1, U$2: TAMURA_L01Z_S05
U$3, U$4: HTFS
U$5, U$6: TAMURA_L06P_S05L06P; TAMURA_L06P_S05

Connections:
GND: C1.2, C2.-, C4.2, C5.2, IC1.11 (V-), IL1_IL2_UDC_TMPHS_VCC.3, IL1_IL2_UDC_TMPHS_VCC.5, IL1_IL2_UDC_TMPHS_VCC.7, R5.1, R8.1, R11.1, R12.1, R13.1, U$1.2 (GND), U$2.2 (GND), U$3.2 (GND), U$4.2 (GND), U$5.P2 (GND), U$6.P2 (GND)
IL1: IC1.8 (OUT), IL1_IL2_UDC_TMPHS_VCC.8, R9.2
IL2: IC1.7 (OUT), IL1_IL2_UDC_TMPHS_VCC.6, R6.2
unnamed: R1.2, R2.1
unnamed: R3.2, R4.1
unnamed: IC1.5 (+IN), IC1.10 (+IN), R13.2, R14.1
unnamed: C1.1, IC1.3 (+IN), R2.2, R5.2
unnamed: B+.1, R1.1
unnamed: B-.1, R3.1
unnamed: IL1_IL2_UDC_TMPHS_VCC.1, L1.1
unnamed: IC1.9 (-IN), R7.2, R9.1
unnamed: IC1.6 (-IN), R6.1, R10.2
unnamed: C3.1, IC1.2 (-IN), R4.2, R15.2
unnamed: C4.1, U$3.4 (VREF)
unnamed: C5.1, U$4.4 (VREF)
unnamed: IC1.12 (+IN), R12.2, TMPHS.1
TMPHS: IC1.13 (-IN), IC1.14 (OUT), IL1_IL2_UDC_TMPHS_VCC.2
UDC: C3.2, IC1.1 (OUT), IL1_IL2_UDC_TMPHS_VCC.4, R15.1
VCC: C2.+, IC1.4 (V+), L1.2, R14.2, TMPHS.2, U$1.3 (VCC), U$2.3 (VCC), U$3.1 (VCC), U$4.1 (VCC), U$5.P3 (VCC), U$6.P3 (VCC)
VOUT1: R7.1, R8.2, U$2.1 (VOUT), U$4.3 (OUT), U$6.P1 (VOUT)
VOUT2: R10.1, R11.2, U$1.1 (VOUT), U$3.3 (OUT), U$5.P1 (VOUT)

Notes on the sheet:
All resistors 1%

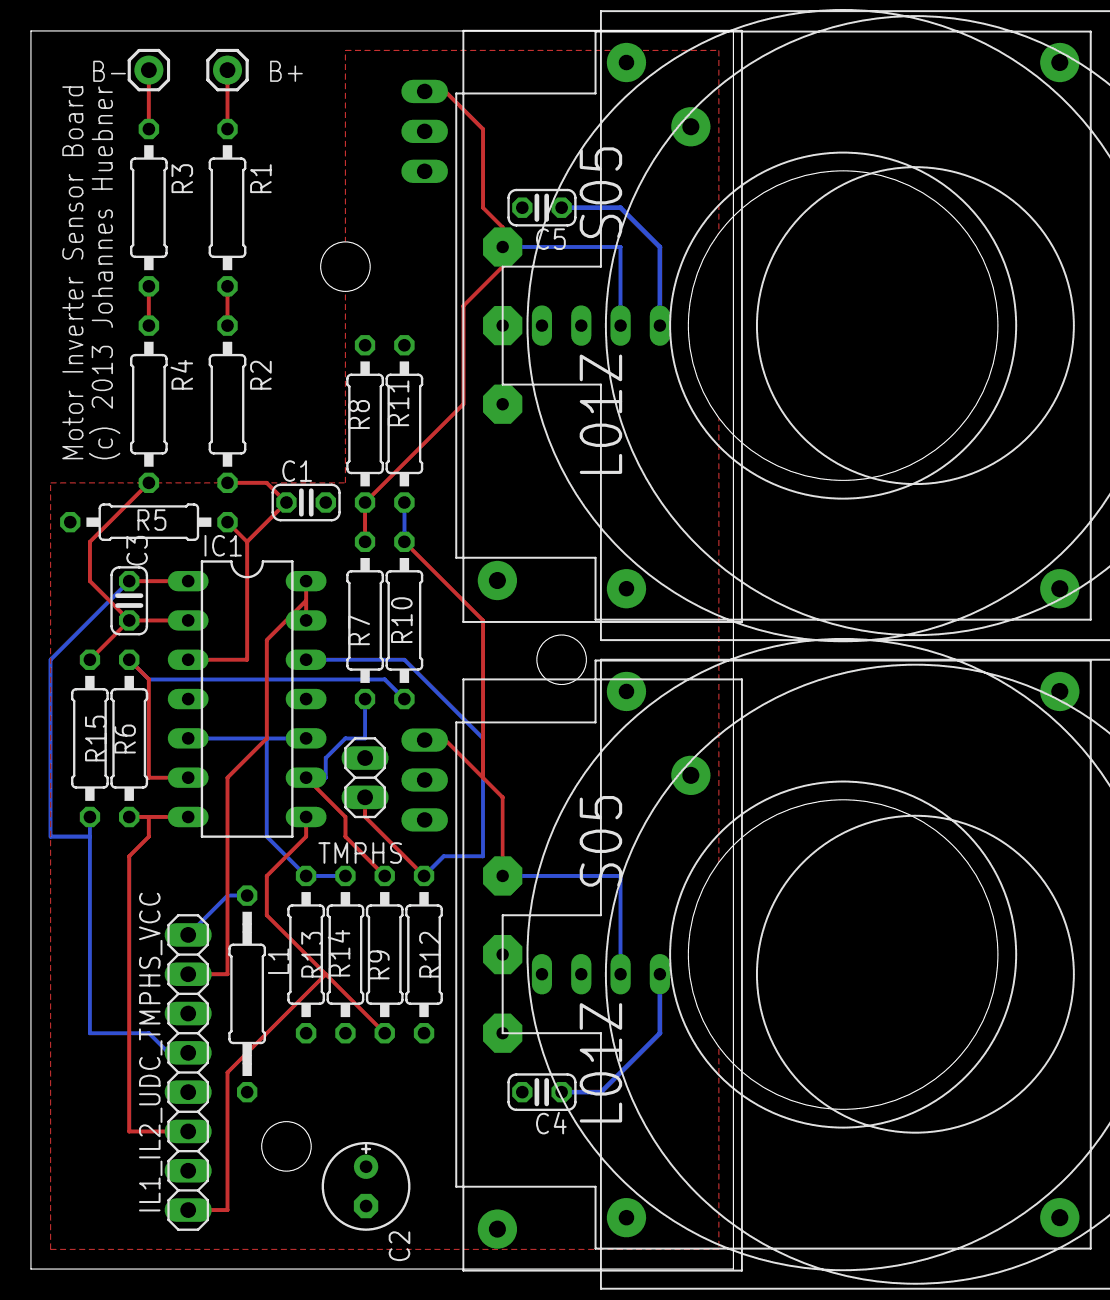
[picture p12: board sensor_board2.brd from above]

Board: 2 copper layers, 45.4 x 80.0 mm, 32 parts (0 on the bottom side), 21 nets.

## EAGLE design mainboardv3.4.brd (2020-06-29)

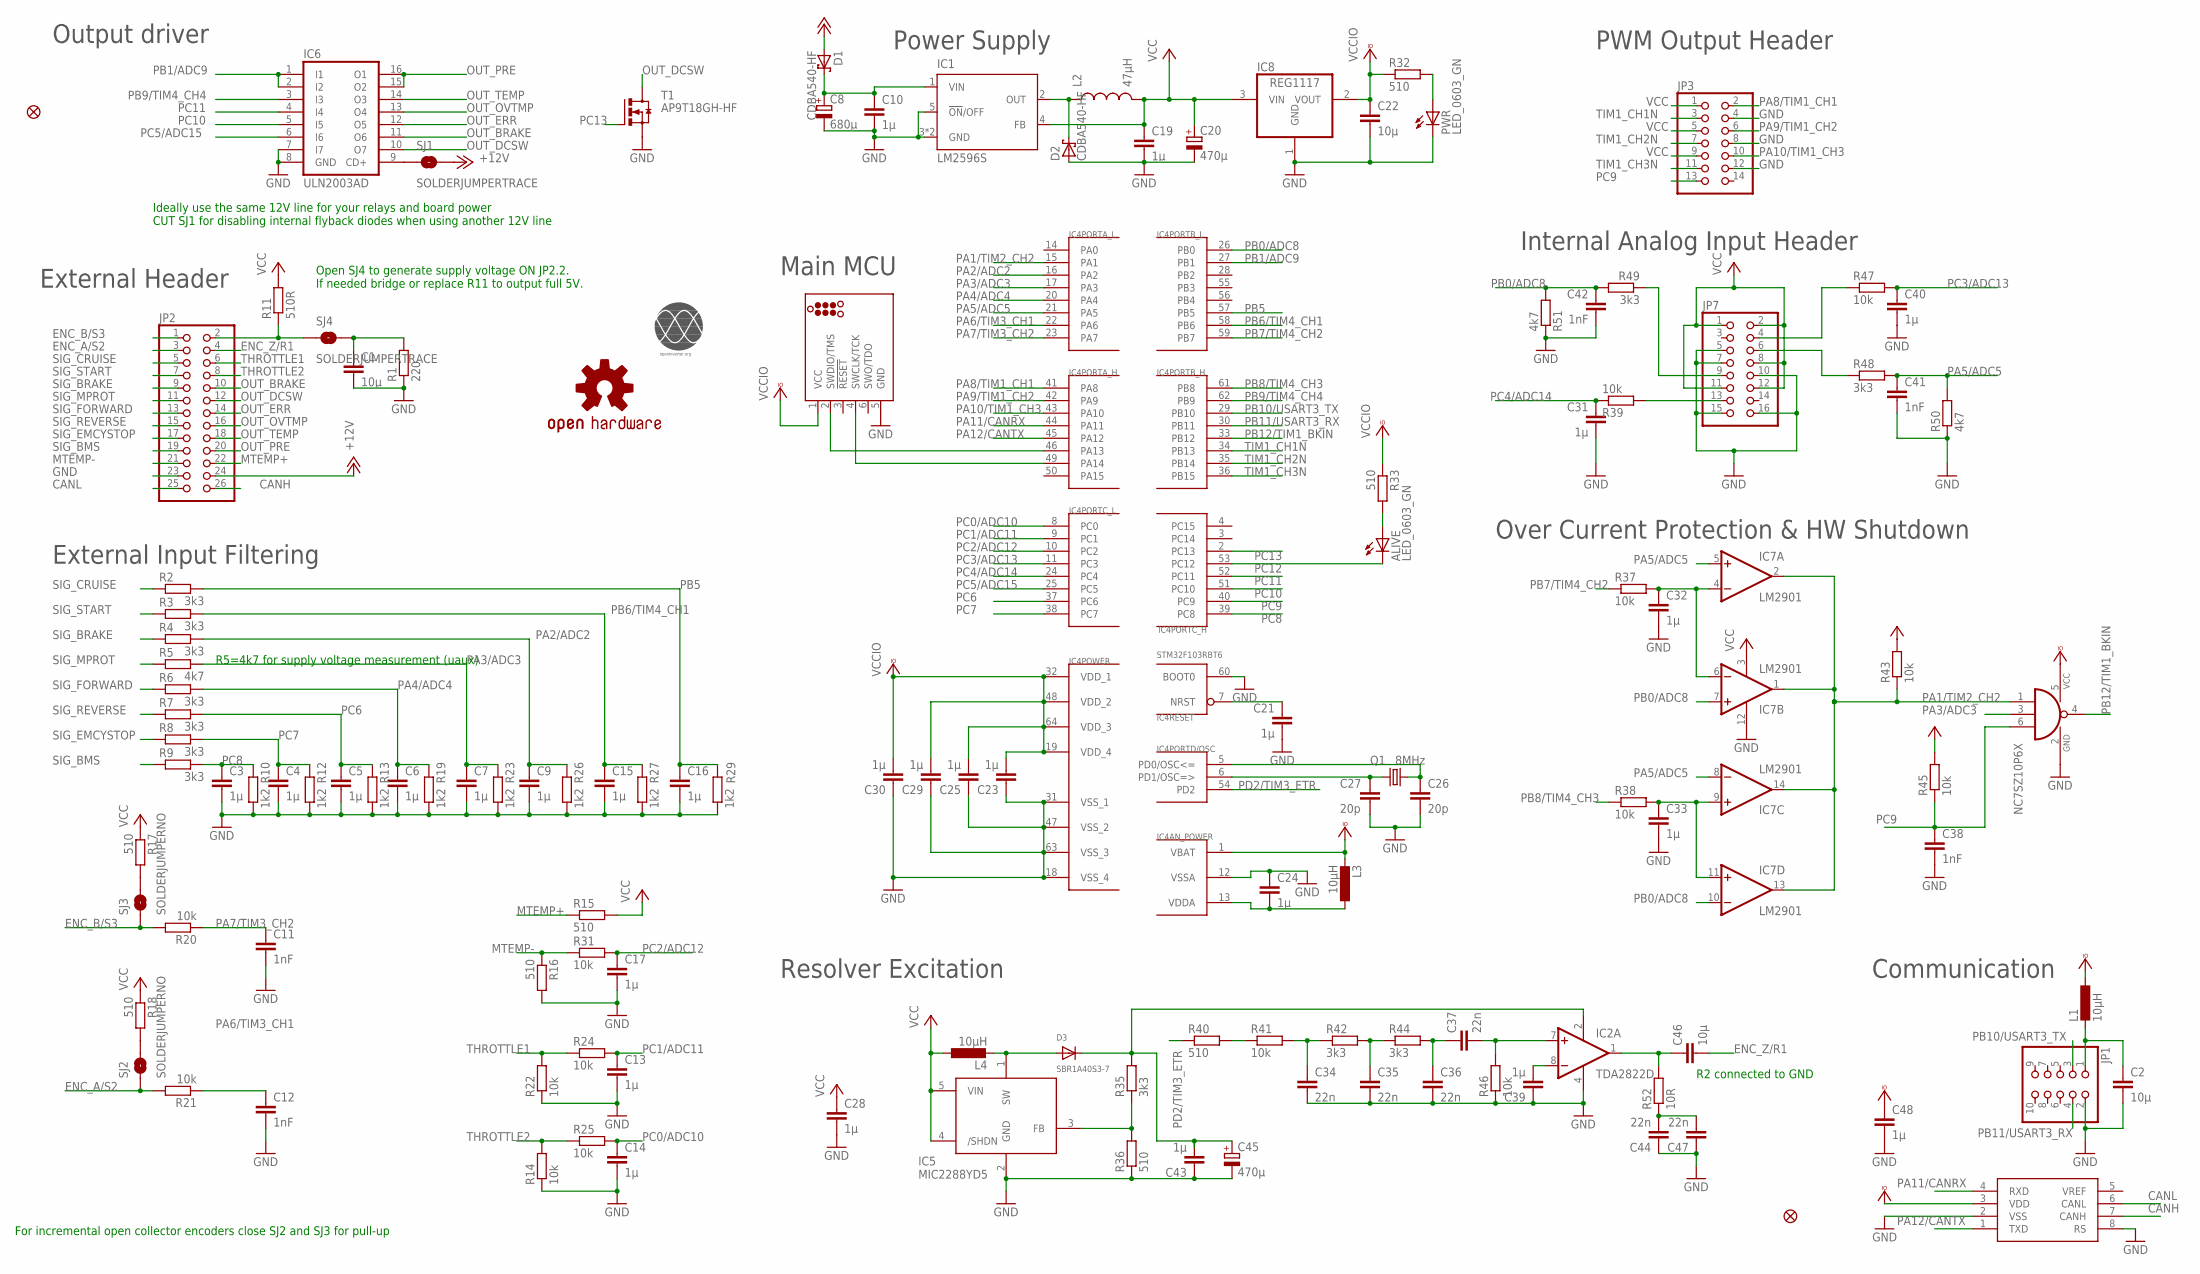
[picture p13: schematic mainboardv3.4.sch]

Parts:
ALIVE: LED_0603_GN; SML0805
C1, C2, C22, C46: 10µ; C0805
C3, C4, C5, C6, C7, C9, C10, C13, C14, C15, C16, C17, C19, C21, C23, C24, C25, C28, C29, C30, C31, C32, C33, C39, C40, C43, C48: 1µ; C0603
C8: 680µ; UD-10X10_NICHICON
C11, C12, C38, C41, C42: 1nF; C0603
C20, C45: 470µ; UD-6,3X7,7_NICHICON
C26, C27: 20p; C0603
C34, C35, C36, C37, C44, C47: 22n; C0603
D1, D2: CDBA540-HF; SMB
D3: SBR1A40S3-7; SOD-323F
FID1, FID2: FIDUCIAL1X2.5; FIDUCIAL-1X2.5
IC1: LM2596S; TO263-5
IC2: TDA2822D; SO08
IC3: SN65HVD230DR; SO08
IC4: STM32F103RBT6; TQFP64
IC5: MIC2288YD5; SOT23-5L
IC6: ULN2003AD; SO16
IC7: LM2901; SO14
IC8: REG1117; SOT223
IC9: NC7SZ10P6X; SC70-6
J1: TC2030_SWD-MCP; TC2030-MCP
JP1: PINHD-2X5/90; 2X05/90
JP2: PINHD-2X13; 2X13
JP3: PINHD-2X7; 2X07
JP7: PINHD-2X8; 2X08
L1, L3: 10µH; L2012C
L2: 47µH; CDRH125
L4: 10µH; L2825P
LOGO1: OSHW-LOGOM; OSHW-LOGO-M
PWR: LED_0603_GN; SML0805
Q1: 8MHz; CRYSTAL-TXC-7A
R1: 220; R0603
R2, R3, R4, R6, R7, R8, R9, R35, R42, R44, R48, R49: 3k3; R0603
R5, R50, R51: 4k7; R0603
R10, R12, R13, R19, R23, R26, R27, R29: 1k2; R0603
R11: 510R; R0603
R14, R20, R21, R22, R24, R25, R31, R37, R38, R39, R41, R43, R45, R46, R47: 10k; R0603
R15, R16, R17, R18, R32, R33, R36, R40: 510; R0603
R52: 10R; R0603
SJ1, SJ4: SOLDERJUMPERTRACE; SJ_2S-TRACE
SJ2, SJ3: SOLDERJUMPERNO; SJ_2S-NO
T1: AP9T18GH-HF; D-PAK_TO252AA
U$1: OI-LOGO; OI_LOGO

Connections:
+12V: D1.A, JP2.24, SJ1.2
CANH: IC3.7 (CANH), JP2.26
CANL: IC3.6 (CANL), JP2.25
ENC_A/S2: JP2.3, R21.2, SJ2.1
ENC_B/S3: JP2.1, R20.2, SJ3.1
ENC_Z/R1: C46.2, JP2.4
GND: C1.2, C2.2, C3.2, C4.2, C5.2, C6.2, C7.2, C8.-, C9.2, C10.2, C11.2, C12.2, C13.2, C14.2, C15.2, C16.2, C17.2, C19.2, C20.-, C21.2, C22.2, C23.1, C24.1, C25.1, C26.2, C27.2, C28.2, C29.1, C30.1, C31.2, C32.2, C33.2, C34.2, C35.2, C36.2, C38.2, C39.1, C40.2, C41.2, C42.2, C43.1, C44.1, C45.-, C47.1, C48.2, D2.A, IC1.3 (GND), IC1.5 (!ON!/OFF), IC1.6 (GND), IC2.4 (V-), IC3.2 (VSS), IC3.8 (RS), IC4.12 (VSSA), IC4.18 (VSS_4), IC4.31 (VSS_1), IC4.47 (VSS_2), IC4.60 (BOOT0), IC4.63 (VSS_3), IC5.2 (GND), IC6.7 (I7), IC6.8 (GND), IC7.12 (GND), IC8.1 (GND), IC9.2 (GND), J1.5 (GND), JP1.2, JP2.23, JP3.4, JP3.8, JP3.12, JP7.5, JP7.7, JP7.10, JP7.15, JP7.16, PWR.C, R1.1, R10.1, R12.1, R13.1, R14.1, R16.2, R19.1, R22.1, R23.1, R26.1, R27.1, R29.1, R36.1, R46.1, R50.1, R51.1, T1.3 (S)
I_L1: JP7.6, R48.1
I_L2: JP7.9, R49.1
MTEMP+: JP2.22, R15.1
MTEMP-: JP2.21, R16.1, R31.1
unnamed: IC6.9 (CD+), SJ1.1
unnamed: C27.1, IC4.6 (PD1/OSC=>), Q1.P$1 (1)
unnamed: R17.2, SJ3.2
unnamed: C26.1, IC4.5 (PD0/OSC<=), Q1.P$2 (2)
unnamed: IC4.46 (PA13), J1.2 (SWDIO/TMS)
unnamed: IC4.49 (PA14), J1.4 (SWCLK/TCK)
unnamed: C24.2, IC4.13 (VDDA), L3.1
unnamed: R18.2, SJ2.2
unnamed: C1.1, R1.2, SJ4.2
unnamed: C33.1, IC7.9 (+IN), IC7.11 (+IN), R38.2
unnamed: C44.2, C47.2, R52.1
unnamed: R40.2, R41.1
unnamed: D2.C, IC1.2 (OUT), L2.1
unnamed: C32.1, IC7.4 (-IN), IC7.6 (-IN), R37.2
unnamed: C35.1, R42.2, R44.1
unnamed: C36.1, C37.1, R44.2
unnamed: C37.2, IC2.7 (+IN), R46.2
unnamed: C46.1, IC2.1 (OUT), R52.2
unnamed: C43.2, C45.+, D3.C, IC2.2 (V+), R35.2
unnamed: PWR.A, R32.2
unnamed: ALIVE.A, R33.2
unnamed: IC5.3 (FB), R35.1, R36.2
unnamed: C8.+, C10.1, D1.C, IC1.1 (VIN)
unnamed: D3.A, IC5.1 (SW), L4.2
unnamed: C39.2, IC2.8 (-IN)
unnamed: C2.1, JP1.1, L1.2
unnamed: C34.1, R41.2, R42.1
NRST: C21.1, IC4.7 (NRST)
OUT_BRAKE: IC6.11 (O6), JP2.10
OUT_DCSW: IC6.10 (O7), JP2.12, T1.4 (D)
OUT_ERR: IC6.12 (O5), JP2.14
OUT_OVTMP: IC6.13 (O4), JP2.16
OUT_PRE: IC6.15 (O2), IC6.16 (O1), JP2.20
OUT_TEMP: IC6.14 (O3), JP2.18
PA1/TIM2_CH2: IC4.15 (PA1), IC7.1 (OUT), IC7.2 (OUT), IC7.13 (OUT), IC7.14 (OUT), IC9.1 (I0), R43.1
PA2/ADC2: C9.1, IC4.16 (PA2), R4.2, R26.2
PA3/ADC3: C7.1, IC4.17 (PA3), IC9.3 (I1), R5.2, R23.2
PA4/ADC4: C6.1, IC4.20 (PA4), R6.2, R19.2
PA5/ADC5: C41.1, IC4.21 (PA5), IC7.5 (+IN), IC7.8 (-IN), R48.2, R50.2
PA6/TIM3_CH1: C12.1, IC4.22 (PA6), R21.1
PA7/TIM3_CH2: C11.1, IC4.23 (PA7), R20.1
PA8/TIM1_CH1: IC4.41 (PA8), JP3.2
PA9/TIM1_CH2: IC4.42 (PA9), JP3.6
PA10/TIM1_CH3: IC4.43 (PA10), JP3.10
PA11/CANRX: IC3.4 (RXD), IC4.44 (PA11)
PA12/CANTX: IC3.1 (TXD), IC4.45 (PA12)
PB0/ADC8: C42.1, IC4.26 (PB0), IC7.7 (+IN), IC7.10 (-IN), R49.2, R51.2
PB1/ADC9: IC4.27 (PB1), IC6.1 (I1), IC6.2 (I2)
PB5: C16.1, IC4.57 (PB5), R2.2, R29.2
PB6/TIM4_CH1: C15.1, IC4.58 (PB6), R3.2, R27.2
PB7/TIM4_CH2: IC4.59 (PB7), R37.1
PB8/TIM4_CH3: IC4.61 (PB8), R38.1
PB9/TIM4_CH4: IC4.62 (PB9), IC6.3 (I3)
PB10/USART3_TX: IC4.29 (PB10), JP1.3
PB11/USART3_RX: IC4.30 (PB11), JP1.4
PB12/TIM1_BKIN: IC4.33 (PB12), IC9.4 (O)
PC0/ADC10: C14.1, IC4.8 (PC0), R25.2
PC1/ADC11: C13.1, IC4.9 (PC1), R24.2
PC2/ADC12: C17.1, IC4.10 (PC2), R31.2
PC3/ADC13: C40.1, IC4.11 (PC3), R47.2
PC4/ADC14: C31.1, IC4.24 (PC4), R39.1
PC5/ADC15: IC4.25 (PC5), IC6.6 (I6)
PC6: C5.1, IC4.37 (PC6), R7.2, R13.2
PC7: C4.1, IC4.38 (PC7), R8.2, R12.2
PC8: C3.1, IC4.39 (PC8), R9.2, R10.2
PC9: C38.1, IC4.40 (PC9), IC9.6 (I2), JP3.13, R45.1
PC10: IC4.51 (PC10), IC6.5 (I5)
PC11: IC4.52 (PC11), IC6.4 (I4)
PC12: ALIVE.C, IC4.53 (PC12)
PC13: IC4.2 (PC13), T1.1 (G)
PD2/TIM3_ETR: IC4.54 (PD2), R40.1
S4/S1: JP2.2, R11.1, SJ4.1
SIG_BMS: JP2.19, R9.1
SIG_BRAKE: JP2.9, R4.1
SIG_CRUISE: JP2.5, R2.1
SIG_EMCYSTOP: JP2.17, R8.1
SIG_FORWARD: JP2.13, R6.1
SIG_MPROT: JP2.11, R5.1
SIG_REVERSE: JP2.15, R7.1
SIG_START: JP2.7, R3.1
THROTTLE1: JP2.6, R22.2, R24.1
THROTTLE2: JP2.8, R14.2, R25.1
TIM1_CH1N: IC4.34 (PB13), JP3.3
TIM1_CH2N: IC4.35 (PB14), JP3.7
TIM1_CH3N: IC4.36 (PB15), JP3.11
TMPHS: JP7.13, R39.2
UDC: JP7.4, R47.1
VCC: C19.1, C20.+, C28.1, IC1.4 (FB), IC5.4 (/SHDN), IC5.5 (VIN), IC7.3 (V+), IC8.3 (VIN), JP3.1, JP3.5, JP3.9, JP7.1, JP7.2, JP7.8, JP7.11, JP7.12, L2.2, L4.1, R11.2, R15.2, R17.1, R18.1, R43.2, R45.2
VCCIO: C22.1, C23.2, C25.2, C29.2, C30.2, C48.1, IC3.3 (VDD), IC4.1 (VBAT), IC4.19 (VDD_4), IC4.32 (VDD_1), IC4.48 (VDD_2), IC4.64 (VDD_3), IC8.2 (VOUT), IC9.5 (VCC), J1.1 (VCC), L1.1, L3.2, R32.1, R33.1

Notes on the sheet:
Output driver
Resolver Excitation
Over Current Protection & HW Shutdown
For incremental open collector encoders close SJ2 and SJ3 for pull-up
R2 connected to GND
Open SJ4 to generate supply voltage ON JP2.2. If needed bridge or replace R11 to output full 5V.
External Input Filtering
Ideally use the same 12V line for your relays and board power CUT SJ1 for disabling internal flyback diodes when using another 12V line
External Header
Communication
Power Supply
PWM Output Header
Internal Analog Input Header
Main MCU
R5=4k7 for supply voltage measurement (uaux)
IC5 MIC2288YD5

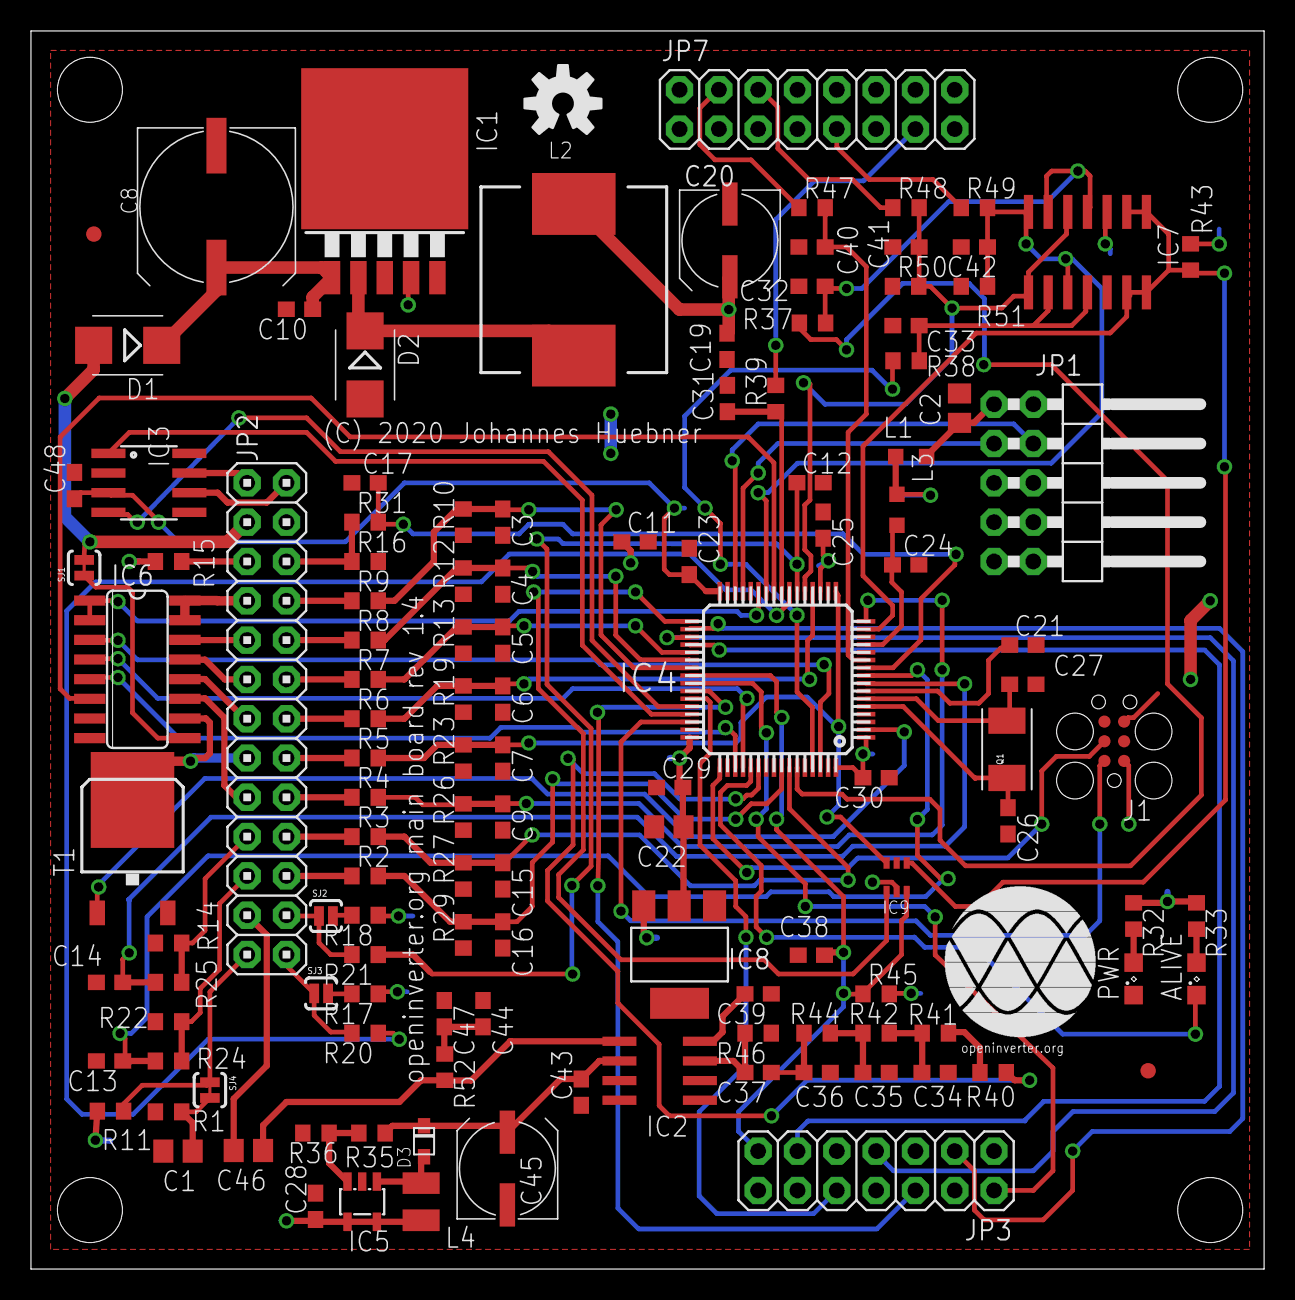
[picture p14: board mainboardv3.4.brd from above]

Board: 2 copper layers, 79.7 x 80.0 mm, 129 parts (0 on the bottom side), 100 nets.

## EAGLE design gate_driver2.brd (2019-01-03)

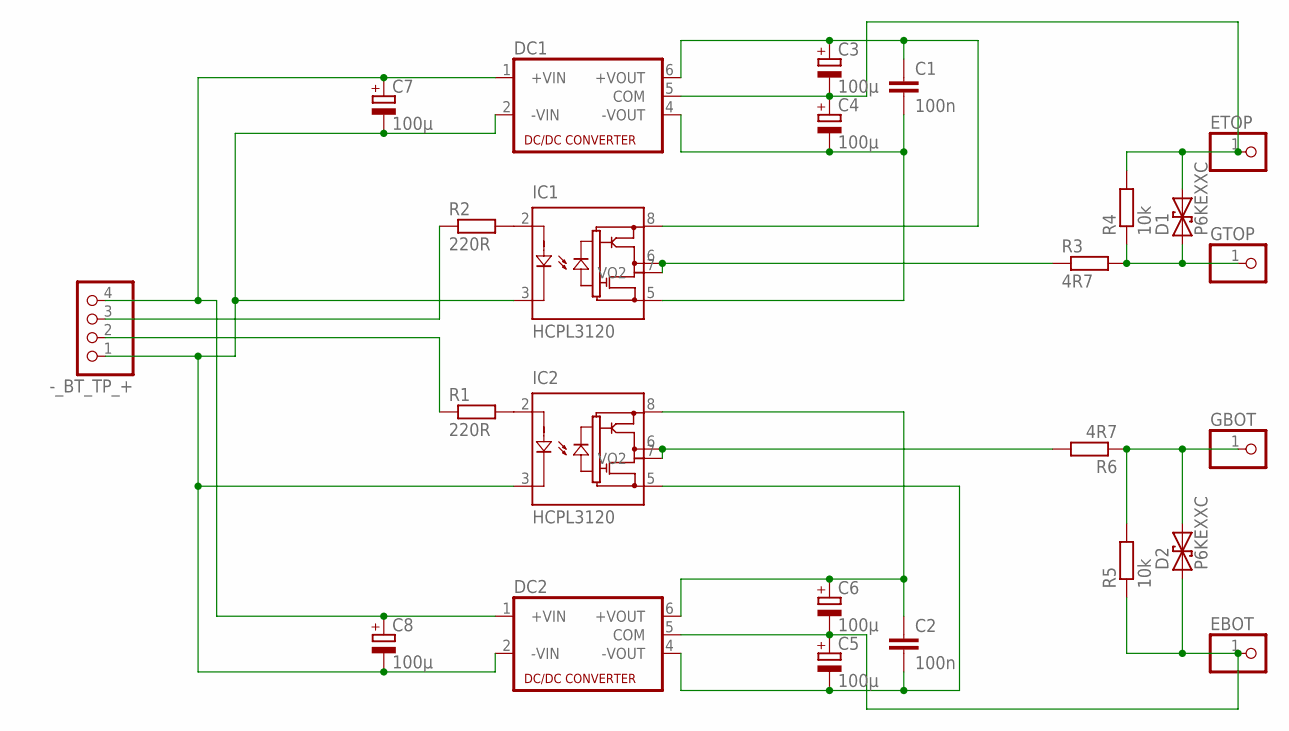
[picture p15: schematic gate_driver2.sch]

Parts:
-_BT_TP_+: PINHD-1X4; 1X04
C1, C2: 100n; C050-025X075
C3, C4, C5, C6: 100µ; E2,5-6E
C7, C8: 100µ; E2,5-5
D1, D2: P6KEXXC; CB417-15
DC1, DC2: NMA
EBOT: PINHD-1X1; 1X01
ETOP: PINHD-1X1; 1X01
GBOT: PINHD-1X1; 1X01
GTOP: PINHD-1X1; 1X01
IC1, IC2: HCPL3120; DIL08
R1, R2: 220R; 0207/10
R3, R6: 4R7; 0309/12
R4, R5: 10k; 0207/10

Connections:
EBOT: C5.+, C6.-, D2.A (1), DC2.5 (COM), EBOT.1, R5.1
ETOP: C3.-, C4.+, D1.C (2), DC1.5 (COM), ETOP.1, R4.2
GBOT: D2.C (2), GBOT.1, R5.2, R6.1
GND: -_BT_TP_+.1, C7.-, C8.-, DC1.2 (-VIN), DC2.2 (-VIN), IC1.3 (CATHODE), IC2.3 (CATHODE)
GTOP: D1.A (1), GTOP.1, R3.2, R4.1
unnamed: IC2.2 (ANODE), R1.2
unnamed: IC1.2 (ANODE), R2.2
unnamed: C1.2, C4.-, DC1.4 (-VOUT), IC1.5 (VEE)
unnamed: C1.1, C3.+, DC1.6 (+VOUT), IC1.8 (VCC)
unnamed: C2.1, C6.+, DC2.6 (+VOUT), IC2.8 (VCC)
unnamed: C2.2, C5.-, DC2.4 (-VOUT), IC2.5 (VEE)
unnamed: IC1.6 (VO), IC1.7 (VO2), R3.1
unnamed: IC2.6 (VO), IC2.7 (VO2), R6.2
unnamed: -_BT_TP_+.4, C7.+, C8.+, DC1.1 (+VIN), DC2.1 (+VIN)
unnamed: -_BT_TP_+.3, R2.1
unnamed: -_BT_TP_+.2, R1.1

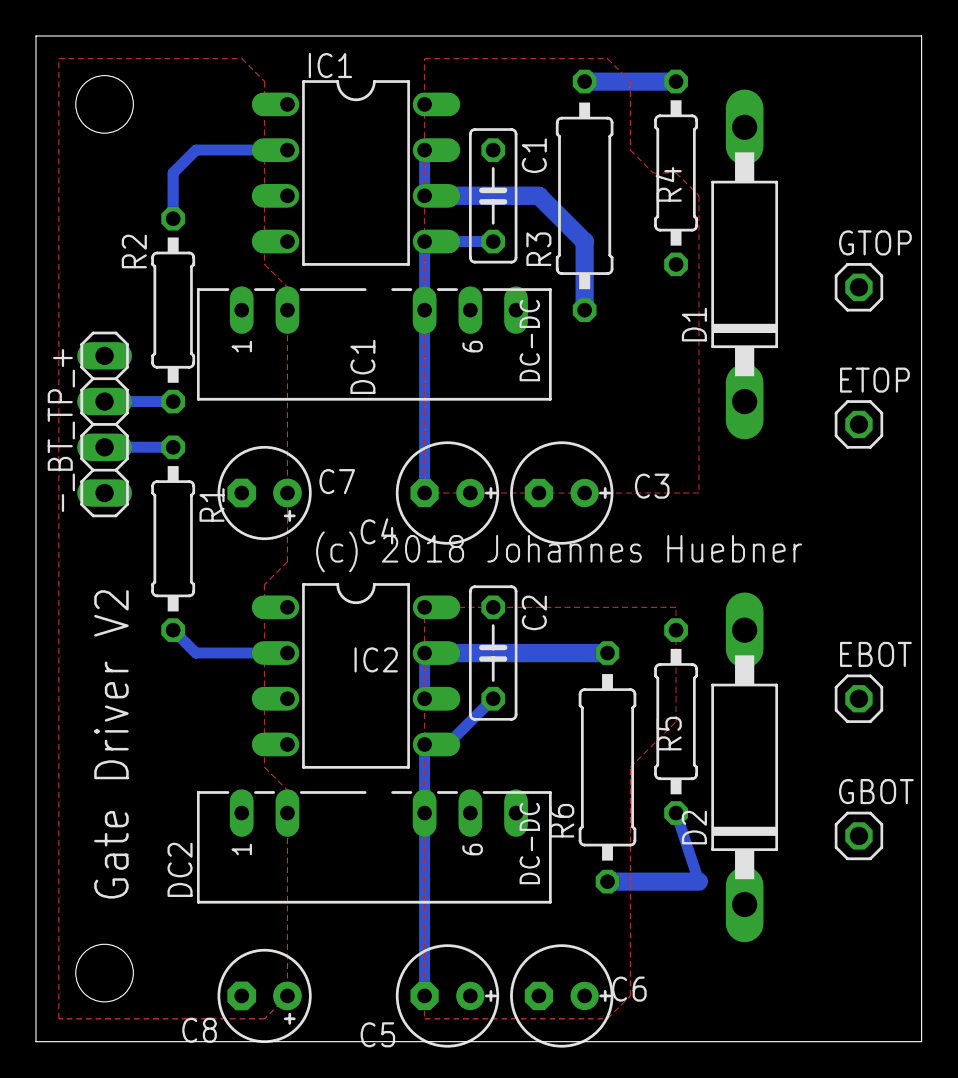
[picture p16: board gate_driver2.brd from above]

Board: 2 copper layers, 49.2 x 55.9 mm, 25 parts (0 on the bottom side), 16 nets.

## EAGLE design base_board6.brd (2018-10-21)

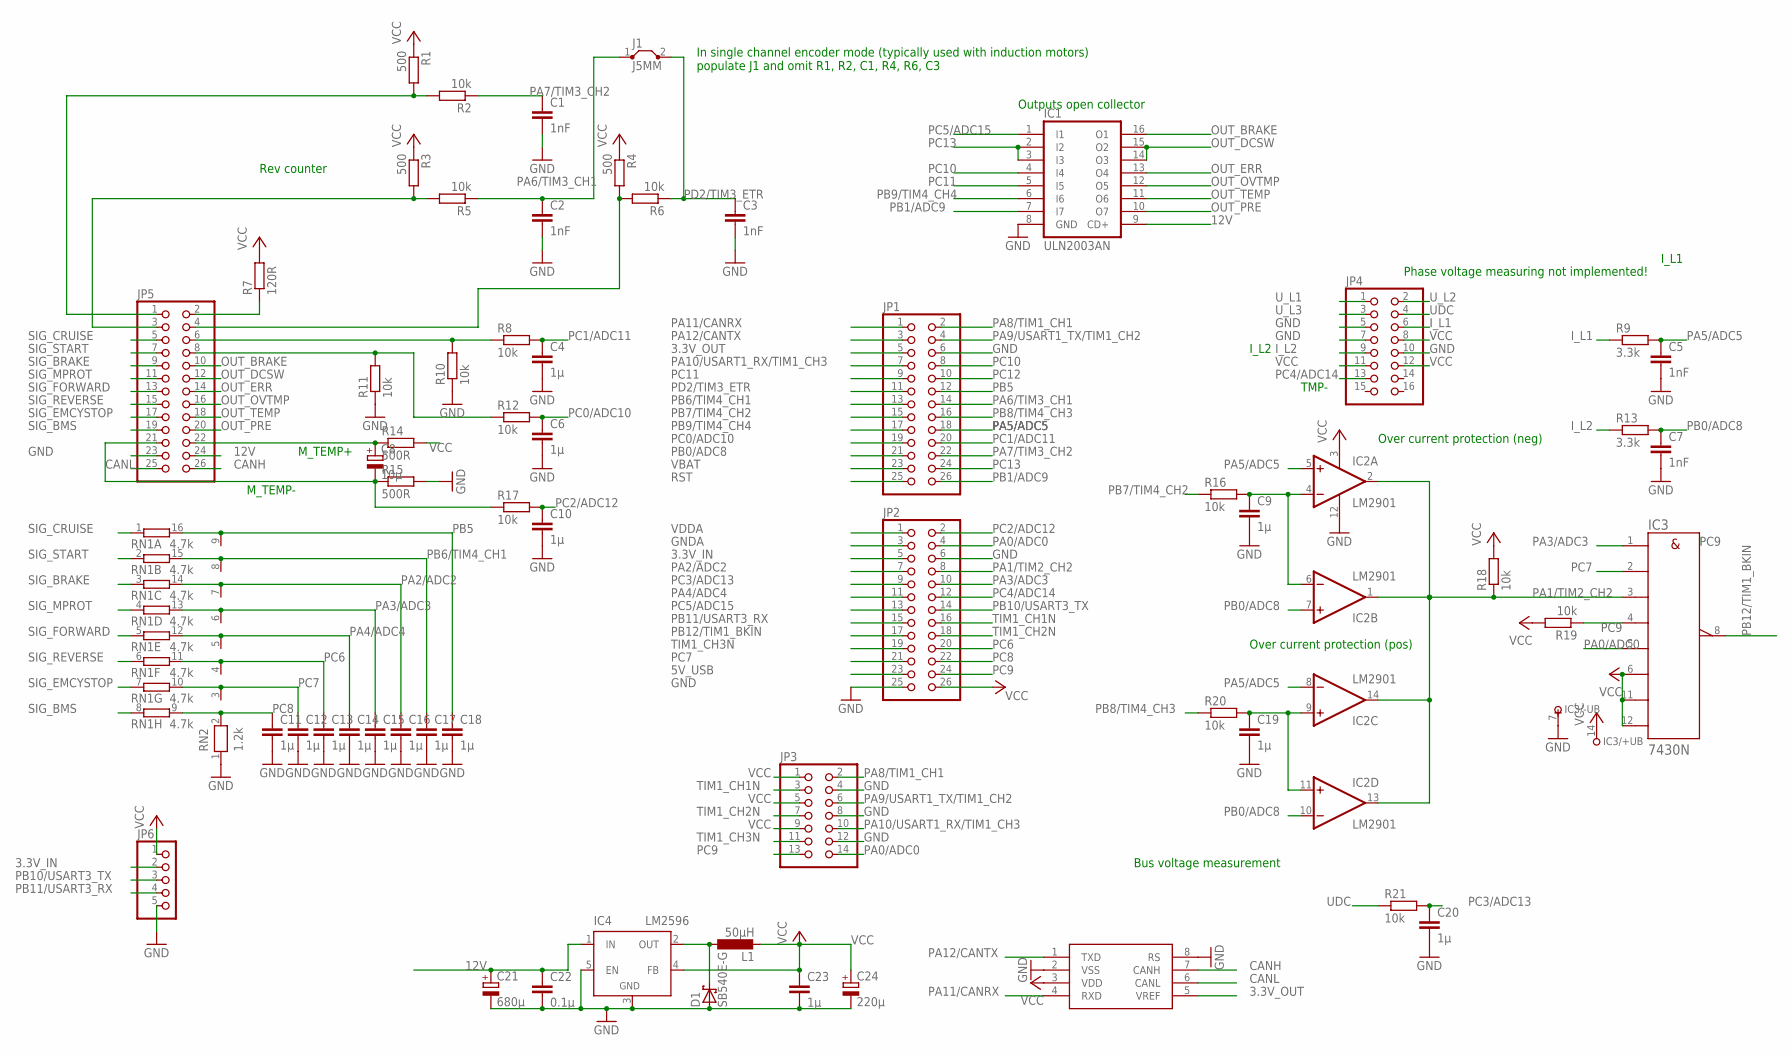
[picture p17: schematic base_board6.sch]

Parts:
C1, C2, C3, C5, C7: 1nF; C025-024X044
C4, C6, C9, C10, C11, C12, C13, C14, C15, C16, C17, C18, C19, C20, C23: 1µ; C025-024X044
C8: 10µ; E2-4
C21: 680µ; E2,5-5
C22: 0.1µ; C050-024X044
C24: 220µ; E2-4
D1: SB540E-G; DO201T15
IC1: ULN2003AN; DIL16
IC2: LM2901; DIL14
IC3: 7430N; DIL14
IC4: LM2596; TO220-51
IC5: MCP2562P; DIL08
J1: J5MM; 05
JP1, JP2, JP5: PINHD-2X13; 2X13
JP3: PINHD-2X7; 2X07
JP4: PINHD-2X8; 2X08
JP6: PINHD-1X5; 1X05
L1: 50µH; TJ3-U1
R1, R3, R4: 500; 0207/10
R2, R5, R6, R8, R10, R11, R12, R16, R17, R18, R19, R20, R21: 10k; 0207/10
R7: 120R; 0207/10
R9, R13: 3.3k; 0207/10
R14, R15: 500R; 0207/10
RN1: 4.7k; DIL16
RN2: 1.2k; RN-9

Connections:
3.3V_IN: JP2.5, JP6.2
3.3V_OUT: IC5.5 (VREF), JP1.5
5V_USB: JP2.23
12V: C21.+, C22.1, IC1.9 (CD+), IC4.1 (IN), JP5.24
CANH: IC5.7 (CANH), JP5.26
CANL: IC5.6 (CANL), JP5.25
GND: C1.2, C2.2, C3.2, C4.2, C5.2, C6.2, C7.2, C9.2, C10.2, C11.2, C12.2, C13.2, C14.2, C15.2, C16.2, C17.2, C18.2, C19.2, C20.2, C21.-, C22.2, C23.2, C24.-, D1.A, IC1.8 (GND), IC2.12 (GND), IC3.7 (-UB), IC4.3 (GND), IC4.5 (EN), IC5.2 (VSS), IC5.8 (RS), JP1.6, JP2.6, JP2.25, JP3.4, JP3.8, JP3.12, JP4.5, JP4.7, JP4.10, JP5.23, JP6.5, R10.1, R11.1, R15.2, RN2.1
GNDA: JP2.3
I_L1: JP4.6, R9.1
I_L2: JP4.9, R13.1
unnamed: JP5.2, R7.1
unnamed: JP5.3, R3.2, R5.2
unnamed: JP5.1, R1.2, R2.2
unnamed: C19.1, IC2.9 (+IN), IC2.11 (+IN), R20.2
unnamed: JP5.4, R4.2, R6.2
unnamed: C8.+, JP5.22, R14.1
unnamed: D1.C, IC4.2 (OUT), L1.1
unnamed: C9.1, IC2.4 (-IN), IC2.6 (-IN), R16.2
unnamed: C8.-, JP5.21, R15.1, R17.1
OUT_BRAKE: IC1.16 (O1), JP5.10
OUT_DCSW: IC1.14 (O3), IC1.15 (O2), JP5.12
OUT_ERR: IC1.13 (O4), JP5.14
OUT_OVTMP: IC1.12 (O5), JP5.16
OUT_PRE: IC1.10 (O7), JP5.20
OUT_TEMP: IC1.11 (O6), JP5.18
PA0/ADC0: IC3.5 (E), JP2.4, JP3.14
PA1/TIM2_CH2: IC2.1 (OUT), IC2.2 (OUT), IC2.13 (OUT), IC2.14 (OUT), IC3.3 (C), JP2.8, R18.1
PA2/ADC2: C16.1, JP2.7, RN1.14 (2), RN2.7
PA3/ADC3: C15.1, IC3.1 (A), JP2.10, RN1.13 (2), RN2.6
PA4/ADC4: C14.1, JP2.11, RN1.12 (2), RN2.5
PA5/ADC5: C5.1, IC2.5 (+IN), IC2.8 (-IN), JP1.18, R9.2
PA6/TIM3_CH1: C2.1, J1.1, JP1.14, R5.1
PA7/TIM3_CH2: C1.1, JP1.22, R2.1
PA8/TIM1_CH1: JP1.2, JP3.2
PA9/USART1_TX/TIM1_CH2: JP1.4, JP3.6
PA10/USART1_RX/TIM1_CH3: JP1.7, JP3.10
PA11/CANRX: IC5.4 (RXD), JP1.1
PA12/CANTX: IC5.1 (TXD), JP1.3
PB0/ADC8: C7.1, IC2.7 (+IN), IC2.10 (-IN), JP1.21, R13.2
PB1/ADC9: IC1.7 (I7), JP1.26
PB5: C18.1, JP1.12, RN1.16 (2), RN2.9
PB6/TIM4_CH1: C17.1, JP1.13, RN1.15 (2), RN2.8
PB7/TIM4_CH2: JP1.15, R16.1
PB8/TIM4_CH3: JP1.16, R20.1
PB9/TIM4_CH4: IC1.6 (I6), JP1.17
PB10/USART3_TX: JP2.14, JP6.3
PB11/USART3_RX: JP2.15, JP6.4
PB12/TIM1_BKIN: IC3.8 (Y), JP2.17
PC0/ADC10: C6.1, JP1.19, R12.2
PC1/ADC11: C4.1, JP1.20, R8.2
PC2/ADC12: C10.1, JP2.2, R17.2
PC3/ADC13: C20.1, JP2.9, R21.2
PC4/ADC14: JP2.12, JP4.13
PC5/ADC15: IC1.1 (I1), JP2.13
PC6: C13.1, JP2.20, RN1.11 (2), RN2.4
PC7: C12.1, IC3.2 (B), JP2.21, RN1.10 (2), RN2.3
PC8: C11.1, JP2.22, RN1.9 (2), RN2.2
PC9: IC3.4 (D), JP2.24, JP3.13, R19.1
PC10: IC1.4 (I4), JP1.8
PC11: IC1.5 (I5), JP1.9
PC12: JP1.10
PC13: IC1.2 (I2), IC1.3 (I3), JP1.24
PD2/TIM3_ETR: C3.1, J1.2, JP1.11, R6.1
RST: JP1.25
SIG_BMS: JP5.19, RN1.8 (1)
SIG_BRAKE: JP5.9, RN1.3 (1)
SIG_CRUISE: JP5.5, RN1.1
SIG_EMCYSTOP: JP5.17, RN1.7 (1)
SIG_FORWARD: JP5.13, RN1.5 (1)
SIG_MPROT: JP5.11, RN1.4 (1)
SIG_REVERSE: JP5.15, RN1.6 (1)
SIG_START: JP5.7, RN1.2 (1)
TIM1_CH1N: JP2.16, JP3.3
TIM1_CH2N: JP2.18, JP3.7
TIM1_CH3N: JP2.19, JP3.11
UDC: JP4.4, R21.1
U_L1: JP4.1
U_L2: JP4.2
U_L3: JP4.3
VBAT: JP1.23
VCC: C23.1, C24.+, IC2.3 (V+), IC3.6 (F), IC3.11 (G), IC3.12 (H), IC3.14 (+UB), IC4.4 (FB), IC5.3 (VDD), JP2.26, JP3.1, JP3.5, JP3.9, JP4.8, JP4.11, JP4.12, JP6.1, L1.2, R1.1, R3.1, R4.1, R7.2, R14.2, R18.2, R19.2
VDDA: JP2.1
X: JP5.6, R8.1, R10.2
Y: JP5.8, R11.2, R12.1

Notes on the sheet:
M_TEMP+
M_TEMP-
TMP-
Over current protection (pos)
Outputs open collector
Phase voltage measuring not implemented!
Bus voltage measurement
Rev counter
Over current protection (neg)
I_L1
I_L2
In single channel encoder mode (typically used with induction motors) populate J1 and omit R1, R2, C1, R4, R6, C3



Board: 2 copper layers, 100.0 x 80.0 mm, 61 parts (3 on the bottom side), 75 nets.

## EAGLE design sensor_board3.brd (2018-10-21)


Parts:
C1, C4, C5: 100nF; C025-024X044
C2: 100µ; E2,5-6E
C3, C6, C7: 1µ; C025-024X044
IC1: TLC274P; DIL14
IC2: ATTINY13DIP; DIP08
L1: 10µ; 0207/12
OK1: PC817; DIL04
PWS1: TME_2405S; TMEXXXXS
R1, R3: 680k; 0207/10
R5, R8, R11, R17: 10k; 0207/10
R6, R9: 82k; 0207/10
R7, R10: 100k; 0207/10
R12: 1.2k; 0207/10
R13: 3.3k; 0207/10
R14: 4.7k; 0207/10
R15, R16: 500; 0207/10
TMPHS: PINHD-1X2; 1X02
U$1, U$2: TAMURA_L01Z_S05
U$3, U$4: HTFS
U$5, U$6: TAMURA_L06P_S05L06P; TAMURA_L06P_S05
VCC_TMPHS_UDC_IL2_IL1: PINHD-1X8; 1X08
X1: W237-102

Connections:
GND: C2.-, C3.1, C4.2, C5.2, C7.1, IC1.11 (V-), PWS1.1 (E-), R8.1, R11.1, R12.1, R13.1, R15.2, U$1.2 (GND), U$2.2 (GND), U$3.2 (GND), U$4.2 (GND), U$5.P2 (GND), U$6.P2 (GND), VCC_TMPHS_UDC_IL2_IL1.3, VCC_TMPHS_UDC_IL2_IL1.5, VCC_TMPHS_UDC_IL2_IL1.7
GND2: C1.2, C6.1, IC2.4 (GND), OK1.2 (C), PWS1.3 (A-), R3.2, R5.1
IL1: IC1.8 (OUT), R9.2, VCC_TMPHS_UDC_IL2_IL1.8
IL2: IC1.7 (OUT), R6.2, VCC_TMPHS_UDC_IL2_IL1.6
unnamed: IC1.5 (+IN), IC1.10 (+IN), R13.2, R14.1
unnamed: C1.1, IC2.7 (PB2(SCK/ADC1)), R1.2, R5.2
unnamed: R1.1, X1.1
unnamed: R3.1, X1.2
unnamed: L1.1, VCC_TMPHS_UDC_IL2_IL1.1
unnamed: IC1.9 (-IN), R7.2, R9.1
unnamed: IC1.6 (-IN), R6.1, R10.2
unnamed: OK1.3 (EMIT), R15.1, R17.2
unnamed: C4.1, U$3.4 (VREF)
unnamed: C5.1, U$4.4 (VREF)
unnamed: IC1.12 (+IN), R12.2, TMPHS.1
unnamed: OK1.1 (A), R16.2
unnamed: IC2.5 (PB0(MOSI)), R16.1
unnamed: C3.2, IC1.3 (+IN), R17.1
TMPHS: IC1.13 (-IN), IC1.14 (OUT), VCC_TMPHS_UDC_IL2_IL1.2
UDC: IC1.1 (OUT), IC1.2 (-IN), VCC_TMPHS_UDC_IL2_IL1.4
VCC: C2.+, C7.2, IC1.4 (V+), L1.2, OK1.4 (COL), PWS1.2 (E+), R14.2, TMPHS.2, U$1.3 (VCC), U$2.3 (VCC), U$3.1 (VCC), U$4.1 (VCC), U$5.P3 (VCC), U$6.P3 (VCC)
VCC2: C6.2, IC2.1 (PB5(NRES)), IC2.8 (VCC), PWS1.4 (A+)
VOUT1: R7.1, R8.2, U$2.1 (VOUT), U$4.3 (OUT), U$6.P1 (VOUT)
VOUT2: R10.1, R11.2, U$1.1 (VOUT), U$3.3 (OUT), U$5.P1 (VOUT)

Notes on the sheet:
All resistors 1%


Board: 2 copper layers, 95.2 x 45.4 mm, 36 parts (0 on the bottom side), 24 nets.

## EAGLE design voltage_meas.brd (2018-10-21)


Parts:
C1, C2, C3: 1µ; C025-024X044
DC/DC: MEV3; NMA
IC1: OPA344; SOT23-5
IC2: SI8920; DIP8
JP1: PINHD-1X2; 1X02
JP2: 22-27-2041-04; 6410-04
R1: 500; 0207/10
R2, R3: 680k; 0207/10
R4, R5, R6, R7: 10k; 0207/10
R8, R9: 1k2; 0207/10
X1: W237-102

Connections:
GND: C2.2, C3.2, DC/DC.2 (-VIN), IC1.5 (V+), IC2.5 (GND), JP1.2, JP2.3, R8.2
GND1: C1.2, DC/DC.4 (-VOUT), IC2.3 (AIN), IC2.4 (GND2), R1.1, X1.1
unnamed: IC2.2 (AIP), R1.2, R2.2
unnamed: R2.1, R3.2
unnamed: R3.1, X1.2
unnamed: IC2.7 (AOP), R4.1
unnamed: IC2.6 (AON), R5.1
unnamed: IC1.1 (OUT), JP2.2, R6.2
unnamed: IC1.4 (-IN), R5.2, R6.1
unnamed: IC1.3 (+IN), R4.2, R7.2, R8.1
unnamed: JP1.1, JP2.1, R9.2
VCC: C2.1, C3.1, DC/DC.1 (+VIN), IC1.2 (V-), IC2.8 (VCC), JP2.4, R7.1, R9.1
VCCIO: C1.1, DC/DC.6 (+VOUT), IC2.1 (VCC2)

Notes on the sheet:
Read Errata #2!


Board: 2 copper layers, 63.2 x 27.9 mm, 18 parts (0 on the bottom side), 13 nets.

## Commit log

2018-11-01 Added openinverter library
    Contains foot print for SMD mainboard. Lets you design an adapter board
2019-01-03 Added gate driver schematics and layout
    [gate_driver2.brd, gate_driver2.sch]
2020-01-03 Added openinverter V3 SMD mainboard revision 1.2
    [mainboardv1.2.brd, mainboardv1.2.sch]
2020-01-03 Added revision info
    [mainboardv1.2.brd]
2020-01-25 Small changed for compatibility with JLCPCBs parts library
    [mainboardv1.2.brd, mainboardv1.2.sch]
2020-01-25 Added Gerber, BOM and placement file - NAND gate still has wrong foot print!
    [mainboardv1.2-bom.xlsx, mainboardv1.2-plc.xlsx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]
2020-01-25 Replaced SOT23-6 by SC70-6 foot print for IC9 Moved copyright info away from trace fixed font of silk screen
    [mainboardv1.2-plc.xlsx, mainboardv1.2.brd, mainboardv1.2.sch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]
2020-06-29 New mainboard v3.4 Using TagConnect for programming Using FET for dcsw output Optimized BOM Added solder bridges for optional resistors
    [mainboardv1.2-bom.xlsx, mainboardv1.2-plc.xlsx, mainboardv3.4-bom.xlsx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]
2020-07-15 Added Prius manufacturing files and schematic
    [prius-gen2-v1.0-bom.xlsx, prius-gen2-v1.0-plc.xlsx]
2021-04-08 Added phase module
    [bom.csv]
2021-11-19 Added Leaf adapter BOM and PLC
    [leaf2-bom.xlsx, leaf2-plc.xlsx]
2022-04-09 Added mini mainboard
    [mainboard-mini.brd, mainboard-mini.sch]
2022-07-05 Added 10k resistor to CAN transceiver RS pin
    [mainboard-mini.brd, mainboard-mini.sch]

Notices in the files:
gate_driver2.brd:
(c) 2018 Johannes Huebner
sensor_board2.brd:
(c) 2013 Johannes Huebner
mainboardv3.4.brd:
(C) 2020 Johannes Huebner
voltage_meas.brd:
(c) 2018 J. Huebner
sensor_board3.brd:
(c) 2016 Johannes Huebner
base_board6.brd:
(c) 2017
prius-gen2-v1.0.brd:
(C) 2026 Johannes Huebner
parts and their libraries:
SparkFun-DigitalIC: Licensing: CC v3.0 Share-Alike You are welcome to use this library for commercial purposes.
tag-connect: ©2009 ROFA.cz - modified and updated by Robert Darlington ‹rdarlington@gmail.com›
